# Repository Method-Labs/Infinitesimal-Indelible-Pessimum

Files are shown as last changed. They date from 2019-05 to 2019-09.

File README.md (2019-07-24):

# Infinitesimal Indelible Pessimum
  This is our first rocket. Our small, unforgettable starting point. Our objectives for it are as follows.
  - Create a small model rocket motor which has a flat thrust curve.
  - Create a rocket which uses this motor to reach 1km in height.
  - Use a flight computer to log data throughout the flight.

  The idea behind this rocket is begin to understand the fundementals of model rocketry, and move on to greater and better things with a strong knowledge base.

## Specifications
  The current specifications are as follows:
  - D Class Rocket Motor
    * 7 x 2.2cm
    * Ammonium Perchlorate and Aluminum Powder Propellant
    * Cylindrical Block Grain Geometry
    * Built-In Nozzle
  - Flight computer
    * STM32F103C8T7 MCU
    * BMP280 Barometer
    * MPU6050 IMU
    * W25Q32FV Memory Chip
    * 1 Pyro Channel
  - Construction Paper Body
  - 20cm Parachute

## Other Parameters
  - Stability > 0.5
  - Burn Time > 1 sec
  - 10ns < Total Impulse < 20ns

## Target Performance
  Targeted performance numbers are as follows:
  - Over 1000 m apogee.
  - Over 200 m/s top speed.

## Milestones
  We have set a few milestones to complete throughout this project in order to ensure proper conduct and a higher chance of success:
  1. Finalize rocket motor design.
  2. Finalize rocket design.
  3. Complete flight computer program.
  4. Complete testing of prototype flight computer.
    * This flight computer will have all the capabilities of the full flight-article flight computer, but will be built with breakout boards and solderless breadboards as opposed to a PCB. It is meant to test the capabilities of a flight computer while not requiring the investment both in terms of time and money that a full flight-ready computer will require.
  5. Complete recovery system deployment testing and validation. The testing procedure will be as follows:
    1. For tests 1-5, the recovery system will be independently tested on the ground with only the flight computer hooked up. There nust be an 80% or higher success rate to pass onto the final 5 tests.
      * Success Criteria: successful nosecone separation and parachute ejection.
    2. For tests 6-10, the recovery system will be integrated with the rest of the rocket, including the flight computer and a mass simulator substitute for the rocket motor. The mass simulator can be anything with roughly the same size and mass as the flight article rocket motor. The rocket will be dropped from a height of two stories (King's Academy Clock Tower is perfect for this). Tests 6 and 7 will not be parachute tests, where the parachute will be pre-deployed and the flight computer is inactive. While tests 8-10 will be full tests where the flight computer is active and responsible for deployment.
      * Success Criteria: successful deployment of recovery system and successful soft touchdown.
  6. Complete preliminary static fire tests with the rocket motor and no instrumentation. 1 nominal test is required before passing this milestone.
    * Success Criteria: The motor is intact throughout the test and burn time is near expected value within reason.
      * <5% Deviance: Nominal performance.
      * <10% Deviance: Acceptable performance, investigation should be undertaken but tests can continue as scheduled.
      * \>10% Deviance: Unacceptable performance, investiagtion should be undertaken and tests are to be suspended.
  7. Complete static fire tests with instrumentation and testing equipment.
    * Success Criteria: Motor thrust curve is as expected within reason. Test data will be run with regressional analysis in relation to the expected curve.
      * r > 0.9: Nominal performance.
      * r > 0.7: Acceptable performance, ivestigation should be undertaken but tests can continue as scheduled.
      * r < 0.7: Unacceptable performance, investagion should be undertakenand tests are to be suspended.
  
### Launch day
  Launch day is currently targeted NET Septeber 2019. Launch conditions are as follows:
  * Wind-speed <= 11 km/h.
  * Turbulence <= 10%.
  * 15C < Temperature < 40C

  Launch operations are as follows:
  * T - 1 hour: All equipment is on-site and ready to go.
  * T - 30 minutes: All equipment is set up and operational
  * T - 10 minutes: Ignition system is armed. Final systems check (go no-go procedure).
  * T - 5 minutes: Evacuate the launch area and a 10 meter circle around it. If exclusion zone is violated, countdown resets here.
  * T - 1 minute: Final countdown begins, all cameras rolling.
  * T - 2 seconds: Ignition.
  * T0: Liftoff.

  Recovery operations are as follows:
  * A set of binoculars are used to keep track of the rocket throughout the launch procedure.
  * At parachute deployment, the rocket's rough position will be clear, and the recovery team should begin moving towards it.
  * At touchdown, the recovery team should approach the landing site, but be 5 meters away from the rocket at the closest. They will be equipped with a fire extinguisher in case some unburned fule burns upon contact with the ground.
  * 2 minutes later, the recovery team tests rocket body temperature by touching it. If it's too high, they wait, otherwise, they can handle it and carry it back to the launchsite.

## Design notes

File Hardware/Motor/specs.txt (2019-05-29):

Class: D
Ejection Charge: None
Total Impulse: 20 newton-seconds
Propellant: Ammonium Perchlorate + Aluminum
Chemical Reaction: 10 Al + 6 NH4CLO4 -> 4 AL2O3 + 2 AlCl3 + 12 H2O + 3 N2
Stoichometric Ratio (AL:AP): 10:6
Mass ratio (AL:AP): 1:2.61200815862
Dimensions: 2cm (diamter) * 7cm (length)
Nozzle: Built-in

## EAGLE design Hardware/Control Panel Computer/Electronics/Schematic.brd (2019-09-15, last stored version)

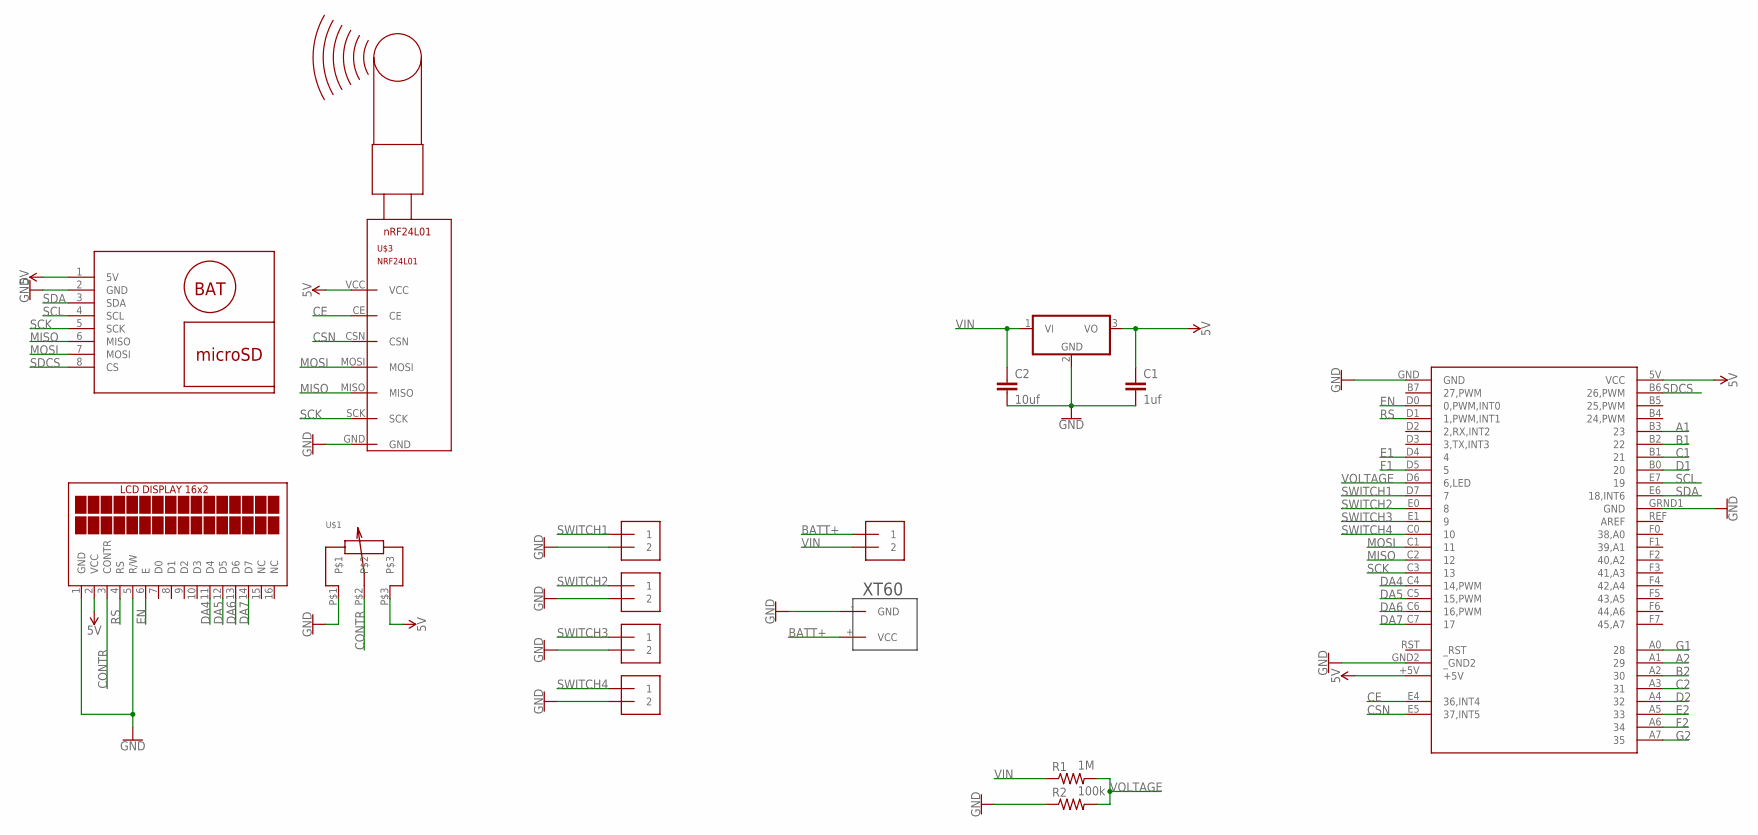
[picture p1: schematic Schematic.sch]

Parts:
C1: 1uf; C025-030X050
C2: 10uf; C025-030X050
DIS1: TUXGR_16X2_R2
IC1: 7805T; TO220H
J1, J2, J3, J4, J5: 1X2-3.5MM
R1: 1M; 0204/5
R2: 100k; 0204/5
U$1: POTENTIOMETER
U$2: XT60
U$3: NRF24L01
U$4: DATA-LOGGER-MINI
U$5: ARDUINO-TEENSY++; TEENSY++

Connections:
5V: C1.1, DIS1.2 (VCC), IC1.3 (VO), U$1.P$3, U$3.VCC, U$4.1 (5V), U$5.5V (VCC), U$5.+5V
A1: U$5.B3 (23)
A2: U$5.A1 (29)
B1: U$5.B2 (22)
B2: U$5.A2 (30)
BATT+: J5.1, U$2.+ (VCC)
C1: U$5.B1 (21)
C2: U$5.A3 (31)
CE: U$3.CE, U$5.E4 (36,INT4)
CONTR: DIS1.3 (CONTR), U$1.P$2
CSN: U$3.CSN, U$5.E5 (37,INT5)
D1: U$5.B0 (20)
D2: U$5.A4 (32)
DA4: DIS1.11 (D4), U$5.C4 (14,PWM)
DA5: DIS1.12 (D5), U$5.C5 (15,PWM)
DA6: DIS1.13 (D6), U$5.C6 (16,PWM)
DA7: DIS1.14 (D7), U$5.C7 (17)
E1: U$5.D4 (4)
E2: U$5.A5 (33)
EN: DIS1.6 (E), U$5.D0 (0,PWM,INT0)
F1: U$5.D5 (5)
F2: U$5.A6 (34)
G1: U$5.A0 (28)
G2: U$5.A7 (35)
GND: C1.2, C2.2, DIS1.1 (GND), DIS1.5 (R/W), IC1.2 (GND), J1.2, J2.2, J3.2, J4.2, R2.1, U$1.P$1, U$2.- (GND), U$3.GND, U$4.2 (GND), U$5.GND, U$5.GND2 (_GND2), U$5.GRND1 (GND)
MISO: U$3.MISO, U$4.6 (MISO), U$5.C2 (12)
MOSI: U$3.MOSI, U$4.7 (MOSI), U$5.C1 (11)
RS: DIS1.4 (RS), U$5.D1 (1,PWM,INT1)
SCK: U$3.SCK, U$4.5 (SCK), U$5.C3 (13)
SCL: U$4.4 (SCL), U$5.E7 (19)
SDA: U$4.3 (SDA), U$5.E6 (18,INT6)
SDCS: U$4.8 (CS), U$5.B6 (26,PWM)
SWITCH1: J1.1, U$5.D7 (7)
SWITCH2: J2.1, U$5.E0 (8)
SWITCH3: J3.1, U$5.E1 (9)
SWITCH4: J4.1, U$5.C0 (10)
VIN: C2.1, IC1.1 (VI), J5.2, R1.1
VOLTAGE: R1.2, R2.2, U$5.D6 (6,LED)

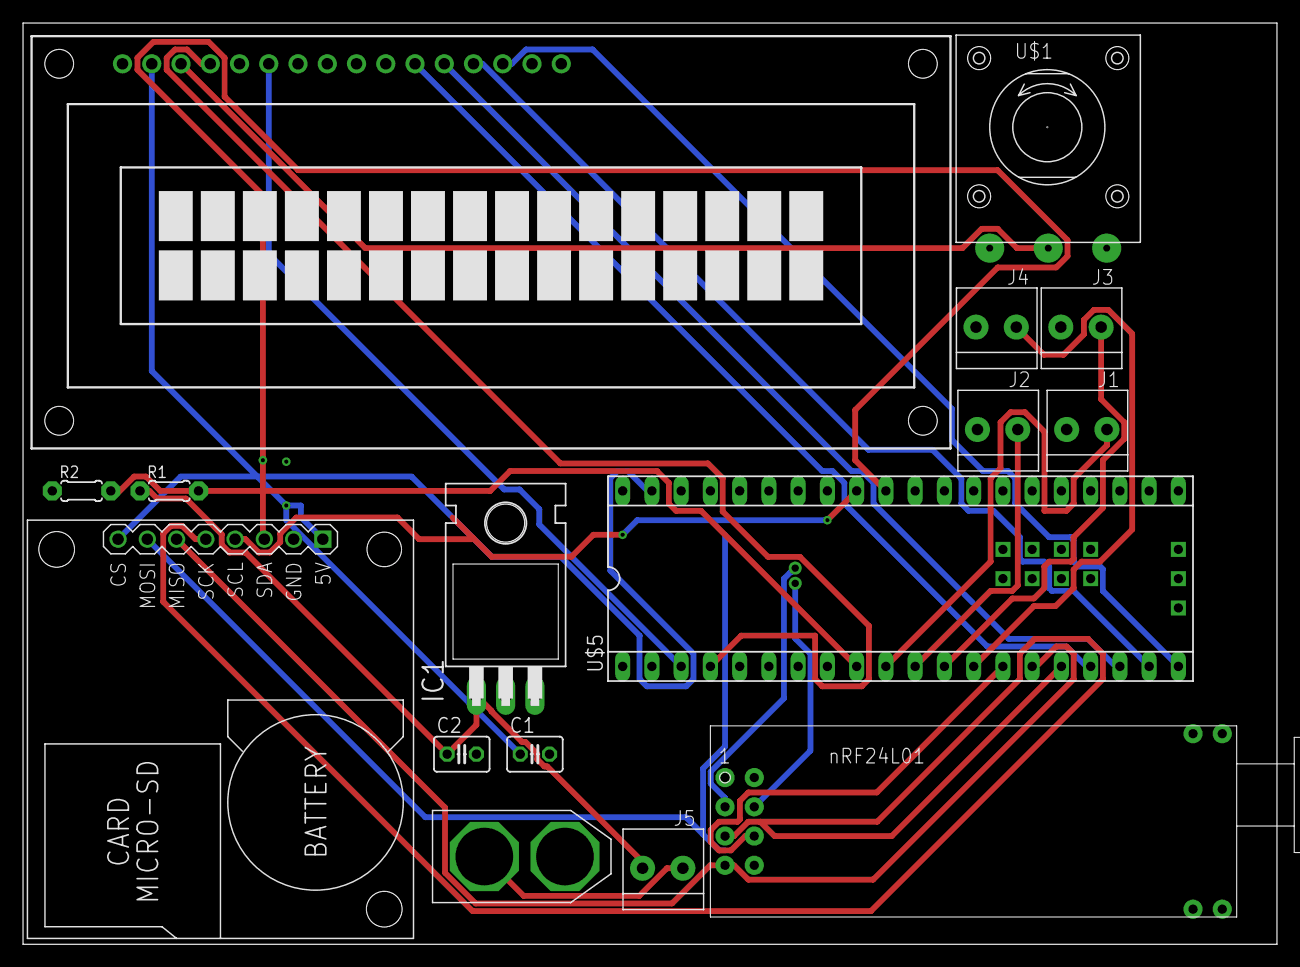
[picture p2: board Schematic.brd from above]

Board: 2 copper layers, 108.9 x 80.0 mm, 16 parts (0 on the bottom side), 24 nets.

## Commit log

2019-05-24 Add OpenRocket file and Milestones to README.md
    [Schematic.fzz]
2019-05-24 Complete Flight Computer Prototpye
    [Prototype.fzz, Schematic.fzz]
2019-05-24 Complete Prototype PCB
    [Prototype.fzz, Schematic.fzz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]
2019-05-27 Remove unnecessary files
    [Prototype.fzz]
2019-05-27 Add basic rocket motor specs
2019-05-29 add flight computer prototype code
2019-05-30 Write flight computer prototype code
2019-05-31 Add calibration code and flight files
2019-05-31 Complete countdown and calibrator objects
2019-06-07 Add materials list
2019-07-21 Add flight computer schematic
    [K-1.sch, Schematic.fzz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]
2019-07-22 Wire voltage regulation and switch circuits and add most nessecary components
    [K-1.sch]
2019-07-22 wire all components in flight computer schematics
    [K-1.sch]
2019-07-23 Change MCU to STM32F103C8T7
    [K-1.sch]
2019-07-23 Added custom MPU Eagle Library
    [K-1.sch]
2019-07-24 Added W25Q32FV Memory Chip through SPI Protocol
    [K-1.sch]
2019-07-24 Update README.md
    Updated MCU, motor and parachute dimensions and memory storage medium
2019-07-24 completed bootloader circuit
    [K-1.sch]
2019-07-26 completed IMU breakout circuit
    [K-1.sch]
2019-08-24 added testing computer code
    [Flight Computer Bootloader.sch, Flight Computer.sch, K-1.sch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]
2019-08-28 Complete Control Panel Computer schematic
    [Flight Computer Bootloader.sch, Flight Computer.sch, Schematic.sch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]
2019-09-15 remove 7-seg displays and complete board design
    [Schematic.brd, Schematic.sch]
2019-09-20 add text to control panel computer PCB
2019-09-21 change control panel processor to STM32 Bluepill
    [Schematic.brd, Schematic.sch]
2019-09-21 fix errors
    [Schematic.brd]
2019-10-08 Completed preliminary motor draft
    [Schematic.brd, Schematic.sch]

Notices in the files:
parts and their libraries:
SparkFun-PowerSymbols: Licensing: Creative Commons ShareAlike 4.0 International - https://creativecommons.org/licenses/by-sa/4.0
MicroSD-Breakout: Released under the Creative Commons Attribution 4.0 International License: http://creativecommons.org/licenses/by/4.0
